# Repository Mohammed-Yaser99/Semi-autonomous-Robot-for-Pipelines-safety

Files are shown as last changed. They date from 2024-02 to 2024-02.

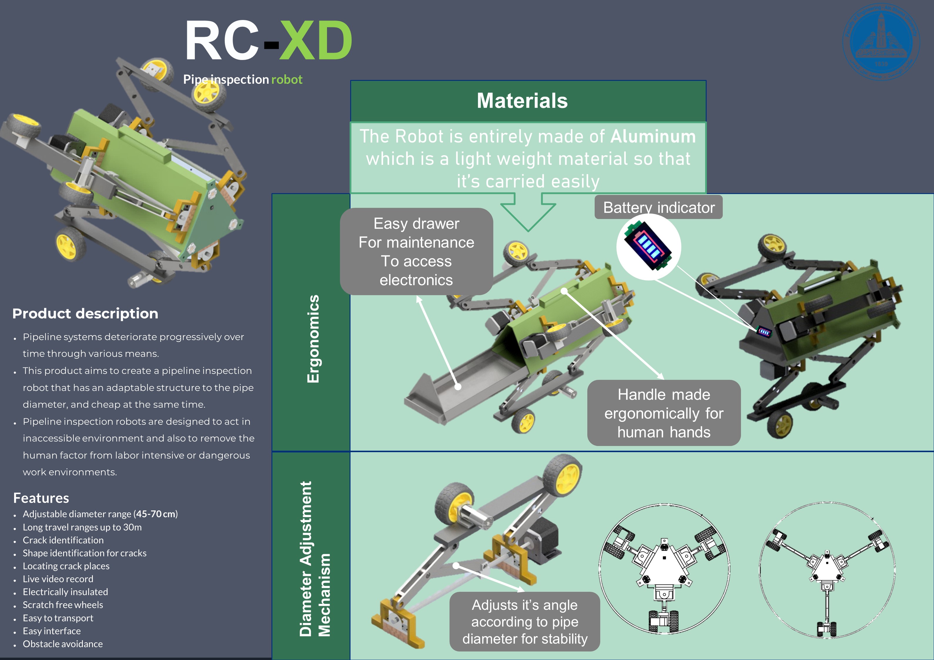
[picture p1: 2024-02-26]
PROJECT's MEDIA/Poster A1-Product Design.jpg

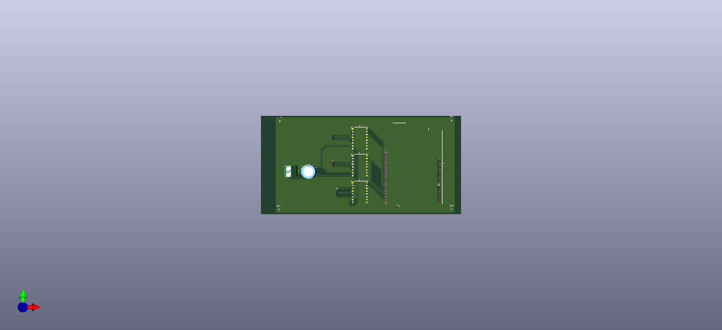
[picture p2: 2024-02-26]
PCB files/Original PCB files ( not manufactured )/pcb 3STEPPERS/3 STEPPERS/FILES/3 STEPPERS.png

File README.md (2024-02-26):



This repository contains working files of a Semi-Autonomous Pipline Inspection robot "RC-XD" :
- Code files for : Arduino mega , Arduino Uno , Rasperry-pi , V-rep simulation
- PCBS design 
- Presenation and Report for detailed aspects and study cases of the project
- Video for the V-rep simulation
  
 
- Pipeline systems deteriorate progressively over time through various means.
- This product aims to create a pipeline inspection robot that has an adaptable structure to the pipe diameter, and cheap at the same time.
- Pipeline inspection robots are designed to act in inaccessible environment and also to remove the human factor from labour intensive or dangerous work environments. 
- Our challenge is to make this robot adaptable to pipe diameters varying from 450mm to 700mm with an adjustable probe mount.

 
- Adjustable diameter range (45-70 cm)
- Long travel ranges up to 30m
- Crack identification 
- Shape identification for cracks 
- Locating crack places
- Live video record 
- Electrically insulated 
- Scratch free wheels and safe to pipes insulation materials 
- Easy to transport 
- Easy interface


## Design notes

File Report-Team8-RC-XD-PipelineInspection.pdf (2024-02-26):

# RESEARCH & PROJECT SUBMISSIONS

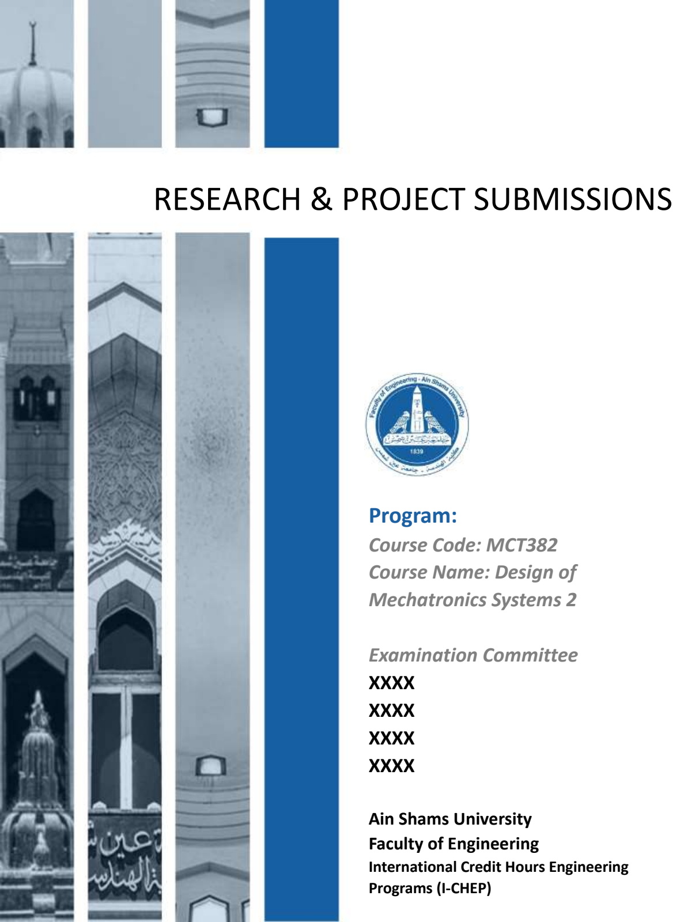
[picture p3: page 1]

SPRING SEMESTER - YEAR 2019/2020

# Program:

## Course Code: MCT382 Course Name: Design of Mechatronics Systems 2

## Examination Committee XXXX XXXX XXXX XXXX

## Ain Shams University Faculty of Engineering

### International Credit Hours Engineering Programs (I-CHEP)

SPRING SEMESTER - YEAR 2019/2020

Student Names:
Mohammed yasser Mohammed
Momen Mohsen
Ahmed Mohammed Nasr

## Student Personal Information for Group Work

## Plagiarism Statement

I certify that this assignment / report is my own work, based on my personal study and/or research and that I have acknowledged all material and sources used in its preparation, whether they are books, articles, reports, lecture notes, and any other kind of document, electronic or personal communication. I also certify that this assignment / report has not been previously been submitted for assessment for another course. I certify that I have not copied in part or whole or otherwise plagiarized the work of other students and / or persons.

Signature/Student Name: | Mohammed Yaser Mohammed
| Momen Mohsen
| Ahmed Mohammed Nasr

Date: 5/5/2021

Student Codes:
17P8214
17P8115
17P8211

AIN SHAMS UNIVERSITY
FACULTY OF ENGINEERING
INTERNATIONAL CREDIT HOURS ENGINEERING PROGRAMS (I-CHEP)

MCT382, Design of Mechatronics Systems 2, SPRING 2020

## Abstract

This report provides basic and advanced operating instructions for the RC-XD Robot. The information in the report will explain the mechanical, electrical and software designs used in this robot, Our vision is to solve some difficulties that pipe inspection companies face, to save the time consumed by manual inspecting procedures and to maintain a safe environment for the employees engaged in this field, Our mission is to improve the quality of the inspecting field in Egypt, to save their time, money and effort and to make robots easily available in the Egyptian market, RC-XD is a pipe inspection robot, it’s main purpose is to inspect the corrosion, cracks , and rust inside the pipes and get its exact position and geometry in the pipe and report it.

## Contents

## List of Figures

## Introduction

Pipeline systems deteriorate progressively over time through various means, so this product aims to create a pipeline inspection robot that has an adaptable structure to the pipe diameter, detects any cracks and cheap at the same time. Pipeline inspection robots are designed to act in inaccessible environment and also to remove the human factor from labour intensive or dangerous work environments. Our challenge is to make this robot adaptable to pipe diameters varying from 450mm to 700mm that can detect any inner cracks in a pipe.

## 1.Market Research

To study the market in Egypt we relied on two sources internet data and face to face meetings with company owners and representatives.

### 1.1. Statistics and surveys

Egyptian market has more than 80 companies in the inspection field excluding petroleum companies, less than 10% of them use robots in their field mainly because it’s too expensive to get a robot from abroad and it’s difficult to maintain it in Egypt.

More than 40% of yearly jobs deal with pipelines with more than 10 meters in length with different diameters ranging from 30cm to 1.2m

A normal inspection job takes 3-4 days in average and average
small companies take 80+ jobs/year.

A technicians’ minimum wage per day ranges from 150 L.E up to 600 L.E, excluding other outlays, so approximately a job with only one technician costs nearly about 2000 L.E

### 1.2. Target

Inspection companies start a job with a site visit to identify what is the required job and take some measurements, then start the solving step which is to brainstorm and think how can they perform this job and what they need, then a preparation step where they gather the required tools and/or operators required, then they start the inspection.

Based on further surveys and meetings, the main target is to eliminate an exhausting and time and money consuming step which is the solving step and eliminating this step will save money, effort and time to a company.

Using these surveys and statistics we concluded how we will shape our robot according to our customers’ needs.

Companies that use robots

Use robots Do not use robots

Figure 1 Companies that use robots relative to all

### 1.3. Value Proposition Canvas

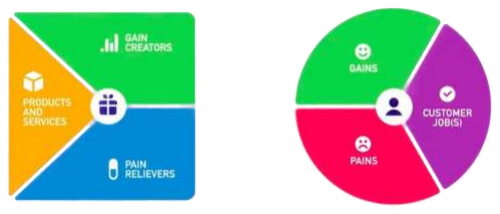
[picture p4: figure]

1.3.1. Gains
- Safe inspection
- Customer Satisfaction
1.3.2. Gain Creators
- Less workers
- Record the inspection process
- More professional method
1.3.3. Pains
- Dealing with hard and extreme cases
- Time and money consuming process
- Unprofessional technicians’ faults
1.3.4. Pain Relievers
- Time efficient
- Less effort
- Adjustable with different diameters
- Crack shape record
1.3.5. Customer Jobs
- Inspection of pipes in oil and gas field
- Case study
1.3.6. Products and Services
- Semi-autonomous
- Adjustable
- Scratch free material
- After sales

Figure 2 Value Proposition canvass

### 1.4. Lean Canvas Model

### 1.5. Academic A1 Poster

Designed for: RC-XD | Designed by: Team 18
Problem 10m+ Length Pipes Diameters variety Insulation Time consuming Existing Alternatives High cost robots Time and money consuming processes | Solution Adjustable Low cost Easy interface Key Metrics Units sold Units rented Contracts | Unique Value Proposition Easy interface Maintenance After Sales Support High-Level Concept | Unfair Advantage Cost Time Channels Sales Team Conferences Company site | Customer Segments Small Gas and Oil inspection companies Early Adopters Below 30 Years old owners
Cost Structure Salaries Development Materials Maintenance | Revenue Structure Contracts Rent Buying

Figure 3 Lean Canvas Model

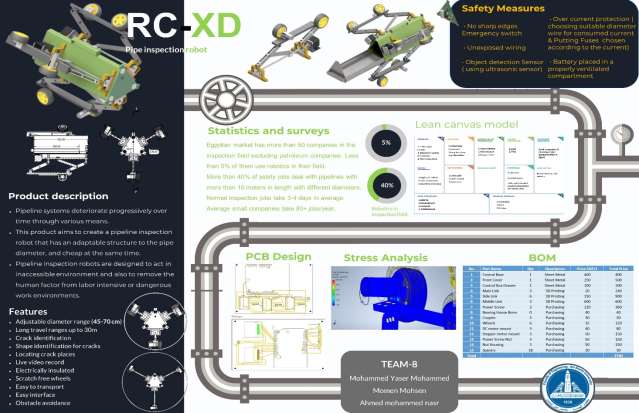
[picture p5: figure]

### 1.6. Product Design A1 Poster

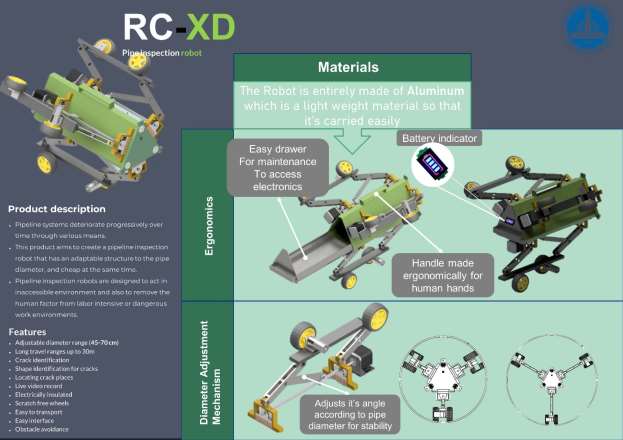
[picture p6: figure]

### 1.5. Brochure

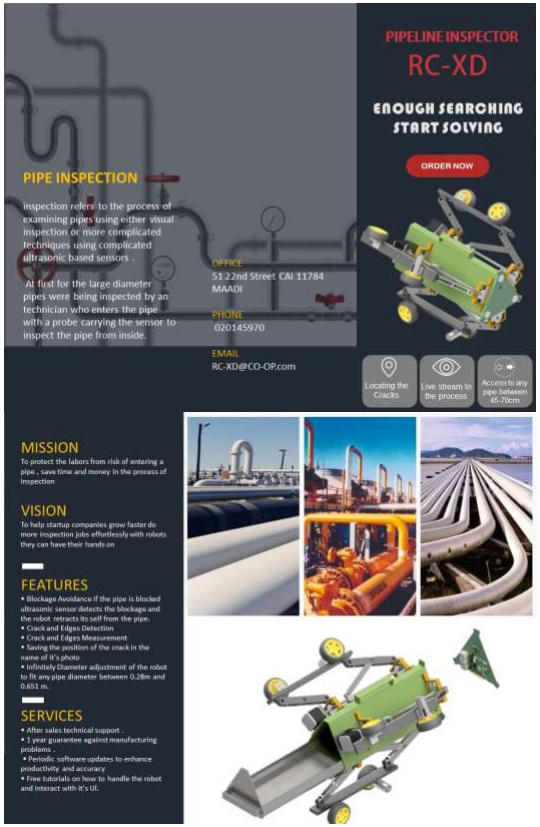
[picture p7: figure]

## 2. Product Description

RC-XD is a semi-autonomous robot that can travel in long pipes with adjustable diameter, scan for inner cracks, locates their locations and identifies the shape of this crack, by setting the pipe diameter, length and the desired travel speed, the robot adjust itself to the pipe diameter and once placed in the pipe it starts to move with the desired speed and begins to scan for any cracks.

RC-XD is a 6 wheeled robot actuated by the four lower wheels, made generally of sheetmetal and do not need an operator to operate it.

### 2.1. Features

- Adjustable diameter range (45-70 cm)
- Long travel ranges up to 30m
- Crack identification
- Shape identification for cracks
- Locating crack places
- Live video record
- Electrically insulated
- Scratch free wheels and safe to pipes insulation materials
- Easy to transport
- Easy interface
- Obstacle avoidance

### 2.2. Environmental Ratings

RC-XD robot is a durable and rugged robot that can be used in harsh environments, well insulated and safe to meet any work site rules.

### 2.3. Main Components

The RC-XD front side contain an ultrasonic sensor behind it the control box which contains the Raspberry Pi, the Arduino uno Launchpad, Lithium ion battery and the PCB, after that we have the main body attached to 3 wheel assemblies with 120⁰ angle between each other -to ensure stability in pipes-each has a mechanism that controls the diameter adjustment. In each mechanism there are 2 wheels, one of those wheels are actuated using a dc motor in the front only, the rest wheels are free to move.

### 2.4. HMI

The user will see the output data as a video feed that can identify any crack and display its dimensions and also the robot will store images of the cracks named with the distance measured and the angle at which the crack was identified

## 3.Mechanical Design

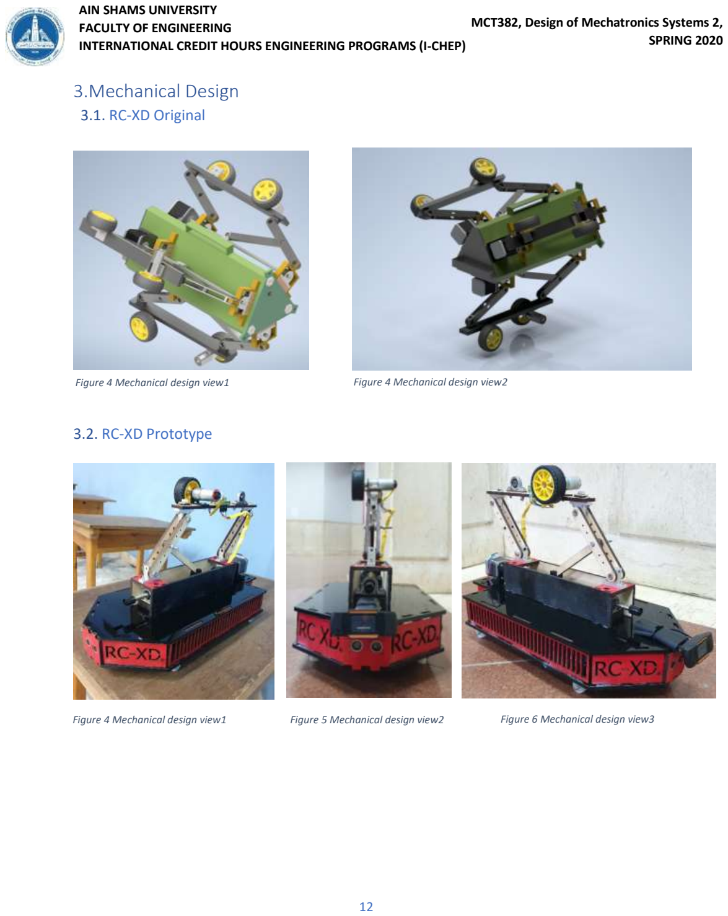
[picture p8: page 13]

### 3.1. RC-XD Original

### 3.2. RC-XD Prototype

Figure 4 Mechanical design view1 | Figure 4 Mechanical design view2
Figure 4 Mechanical design view1 | Figure 5 Mechanical design view2 | Figure 6 Mechanical design view3

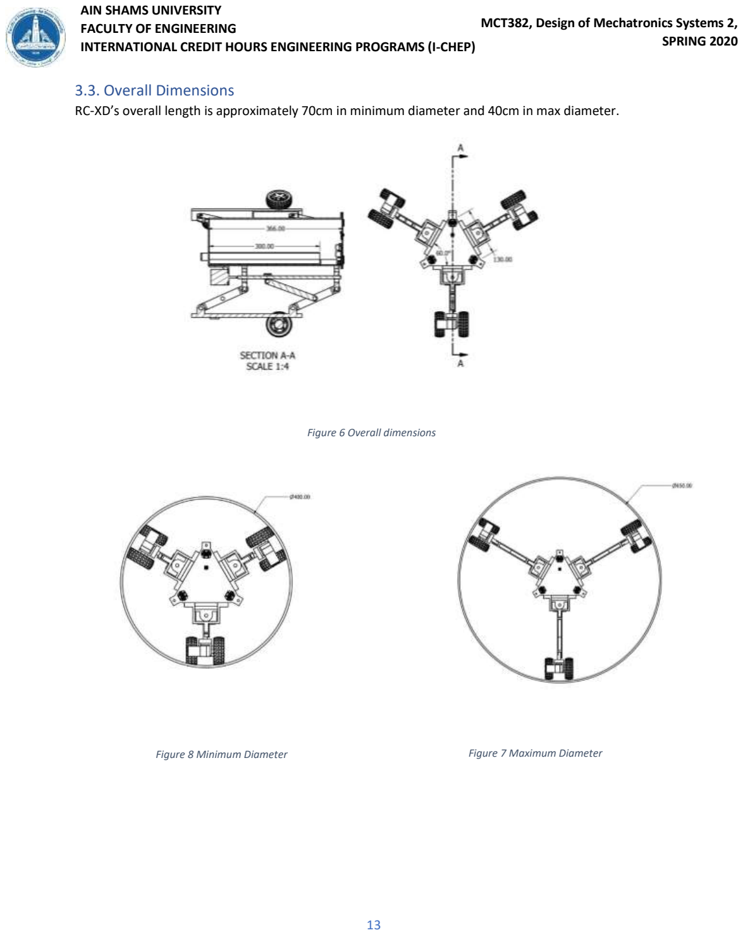
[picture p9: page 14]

### 3.3. Overall Dimensions

RC-XD’s overall length is approximately 70cm in minimum diameter and 40cm in max diameter.

Figure 6 Overall dimensions

Figure 8 Minimum Diameter | Figure 7 Maximum Diameter

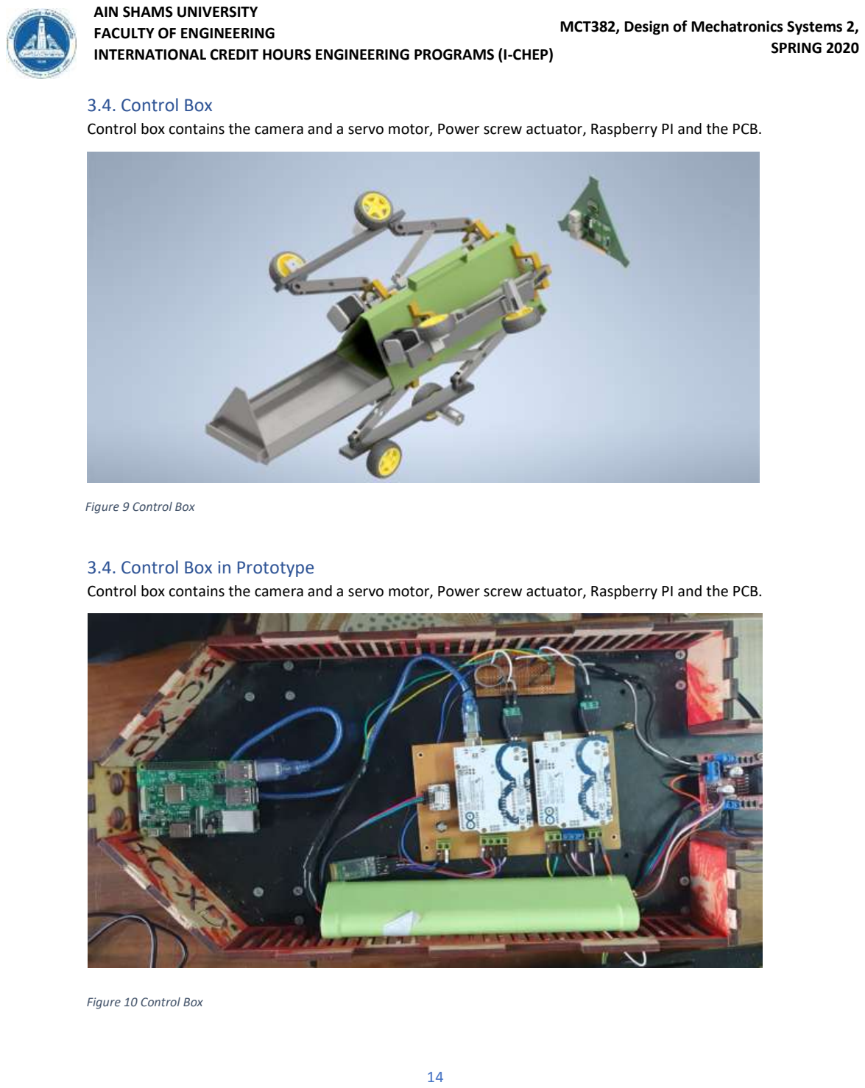
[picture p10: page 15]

### 3.4. Control Box

Control box contains the camera and a servo motor, Power screw actuator, Raspberry PI and the PCB.

### 3.4. Control Box in Prototype

Control box contains the camera and a servo motor, Power screw actuator, Raspberry PI and the PCB.

Figure 9 Control Box

Figure 10 Control Box

### 3.5. Diameter Adjustment Mechanism

In a nutshell it’s a Four-Bar Mechanism actuated by a Four-Bar Mechanism. The power screw actuator receives a signal with the desired diameter, then the power screw rotates with the set angle moving the bushes a certain distance, and the bushed moves a triangular plate attached to it that moves relative to a fixed plate bolted to the base.

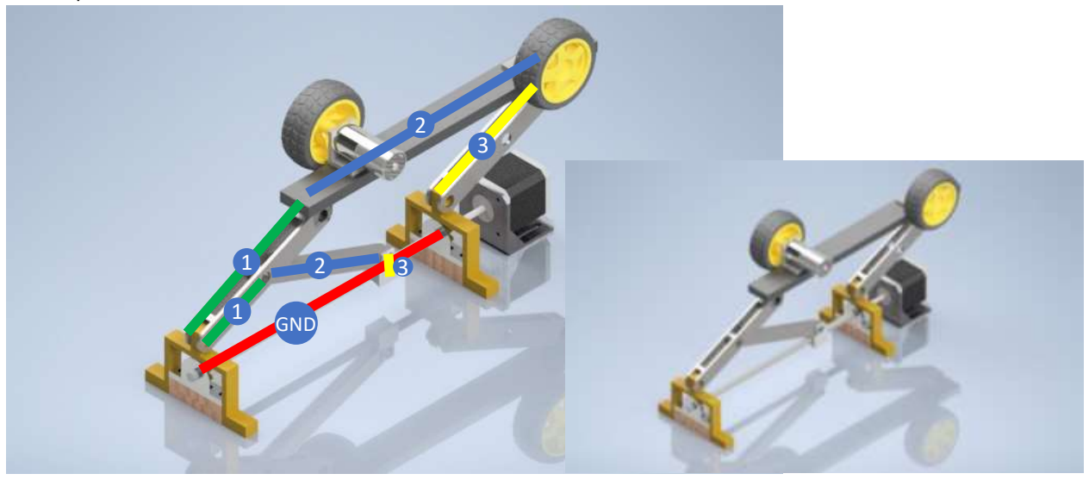
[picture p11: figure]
GND

Attached to the moving plate three links connected to the arms holding the wheels so moving the power screw nut changes the angle of the hinged arms changing the central distance of the wheel.

Figure 13 Diameter Adjustment Mechanism

### 3.6. Stress Analysis

Assuming Worst Case:

- Robot’s weight is 10 kg
- Only two wheel carries the whole weight
- Motor Radial Load = 60 N.m (From datasheet)

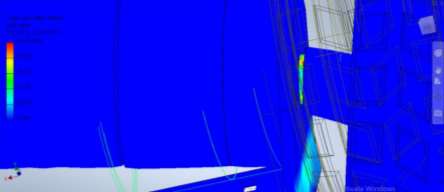
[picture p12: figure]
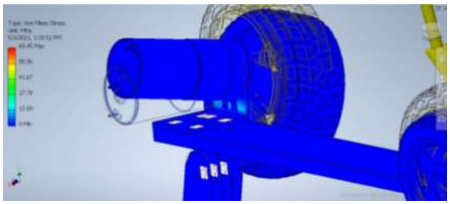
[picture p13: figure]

Figure 14 Stress Analysis

Figure 15 Stress Analysis

### 3.7. Mechanical BOM

No. | Part Name | Qty | Description | Price EGP/1 | Total Price
1 | Central Base | 1 | Sheet Metal | 400 | 400
2 | Front Cover | 1 | Sheet Metal | 250 | 500
3 | Control Box Drawer | 1 | Sheet Metal | 100 | 200
4 | Main Link | 3 | 3D Printing | 20 | 240
5 | Side Link | 6 | 3D Printing | 150 | 900
6 | Middle Link | 3 | 3D Printing | 600 | 600
7 | Power Screw | 3 | Purchasing | 120 | 360
8 | Bearing House 8mm | 0 | Purchasing | 40 | 40
9 | Coupler | 3 | Purchasing | 30 | 30
10 | Wheels | 6 | Purchasing | 15 | 120
11 | DC motor mount | 3 | Purchasing | 40 | 80
12 | Stepper motor mount | 3 | Purchasing | 50 | 150
13 | Power Screw Nut | 3 | Purchasing | 50 | 150
14 | Nut Housing | 3 | Purchasing | 50 | 150
15 | Spacers | 18 | Purchasing | 30 | 30
Total | | | | | 3760
Figure 11 Mechanical BOM

## 4. Electrical Design

Electrical Schematics is designed to fit the operation principles determined and depends on the actuator sizing that was done will be mentioned later, and the selected sensors, so the battery was roughly estimated. And the calculations determined that a 12V battery of 6000mAh is required.

So, to limit the size and weight we decided to use Lithium ions batteries and its characteristics also suits our needs.

### 4.1. Sensors Selection

RC-XD uses five sensors, three encoders for each motor for position feedback, one camera to detect the cracks and an ultrasonic sensor to detect obstacles if there is any.

4.1.2. Raspberry PI Camera NV
Raspberry Pi Night Vision Camera plugs directly into the CSI connector on the Raspberry Pi.

This Raspberry Pi night vision camera uses the same OV5647 as the standard Raspberry Pi camera, and is therefore able to deliver a crystal clear 5MP resolution image, or 1080p HD video recording at 30fps.

4.1.3. DC Motor Encoder
Attached to each DC Motor is an encoder which transmits a set number of electronic pulses for each rotation of its shaft so by using simple mathematical formulas it is easy to calculate the travelled distance.

### 4.2. Actuator Sizing

Estimated total weight from CAD is 10 kg driven by two DC motors and the two actuated wheels have the same parameters and conditions.

Wheel outer diameter = 66 mm

Assumed wheel mass = 0.3 kg

Rolling Coefficient of friction between wheel and pipe = 0.3

Assume all pipes has no inclination.

Assumed fixed speed operation = 2 rad/sec

tacc= 1 sec

Jtot=Jm+Jeff (on each actuated wheel)

### Jactuated wheel = (0.5*m*r^2)=(0.5*0.3* (66 × 10⁻³

/ 2)²

)= 1.6335*10⁻⁴

### kg·m ²

Using kinetic conversion theorem:

### - Jbody = m*r²=10*(66 × 10⁻³

/ 2)²= 10.89*10⁻³

### kg·m ² - Jrolling wheel = 0.5*m*r²= 0.5*0.3* (66 × 10⁻³

/ 2)²= 1.6335*10⁻⁴

### kg·m ²

### Jeff = 1.6335*10⁻⁴

+ 10.89*10⁻³

+ 1.6335*10⁻⁴ = 11.22*10⁻³

### Jtot=Jm+Jeff = 11.22*10⁻³ + 11.22*10⁻³ = 0.02243 kg·m ²

### Tr (assumed resistive torque) = 9.8(5+(0.3*3))*0.3* (66 × 10⁻³

/ 2) = 0.57 Nm

Θ

### acc = 2/0.1=20 rad/sec

### Peak torque required = Tmax = 0.02243*20 + 0.57 = 1.5 Nm

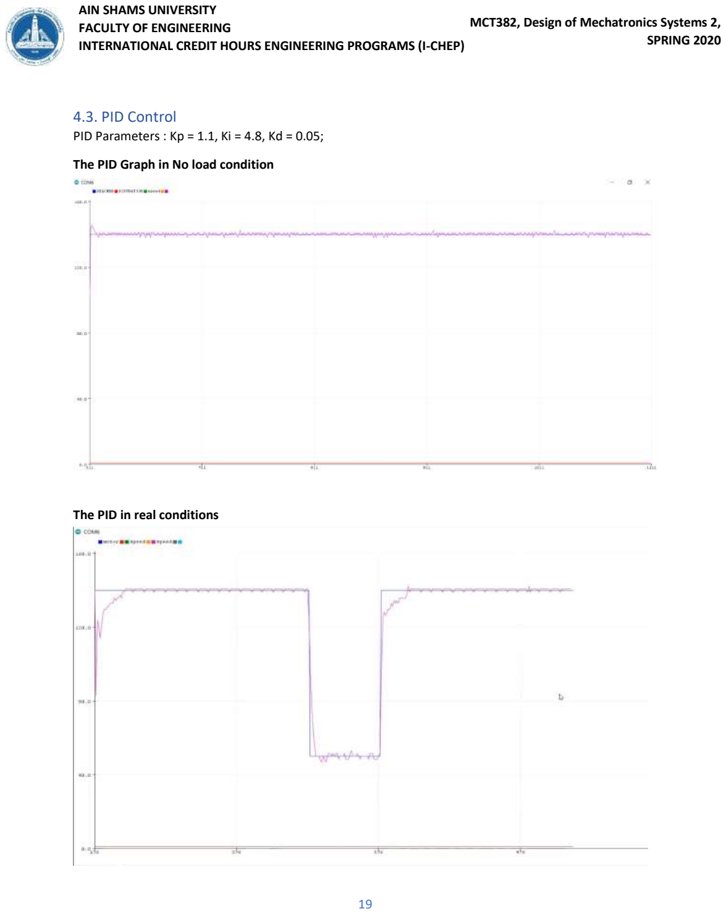
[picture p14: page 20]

### 4.3. PID Control

PID Parameters : Kp = 1.1, Ki = 4.8, Kd = 0.05;

The PID Graph in No load condition

The PID in real conditions

### 4.4. Battery Sizing

Average current draw by each component:

- | Arduino uno board | 0.05 A
- | Raspberry pi | 2.5 A
- | Three driving DC motors | 3.5 A
- | Power screw three Stepper motor | 5.25 A
- | Ultrasonic sensor | 0.015A
- | Camera | 0.5A

For motors I(amp) = (Nω*2π/V*60)

Consumed Power = ((0.05+2.5+0.015+0.5)*5) +((3.5+5.25)*12) = 120 W

Assumed total power losses 10 W

Total power = 130 W

Battery Voltage 12V

Total current = 10 A

Operating time 30 minutes

### Battery size needed = 5 Ah

### 4.5.PCB Design

4.5.1. PCB Schematic

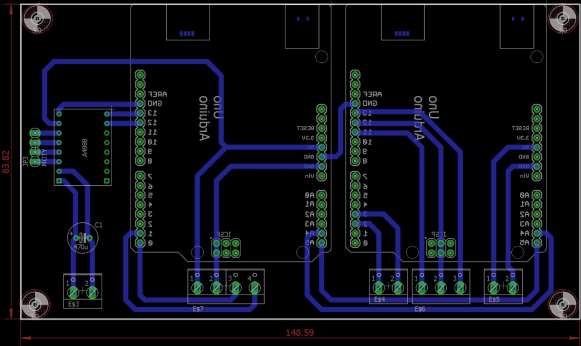
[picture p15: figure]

4.5.2. Communication Protocols
- Arduino1 controls the stepper motor and the bluetooth module
- Arduino2 controls the Dc Motors with the pid control
- Raspberry pi controls the camera with the image processing

We tried to optimize our resources and use the different communication protocols available in the uno. So Arduino1 takes the diameter and distance commands from a mobile application using the Bluetooth module using UART, then it sends the data to Arduino2 using I2C protocol to begin moving the report, and in parallel the raspberry pi vision module works and when a crack is detected it sends a character to Arduino2 using UART to slow down to be able to see the crack.

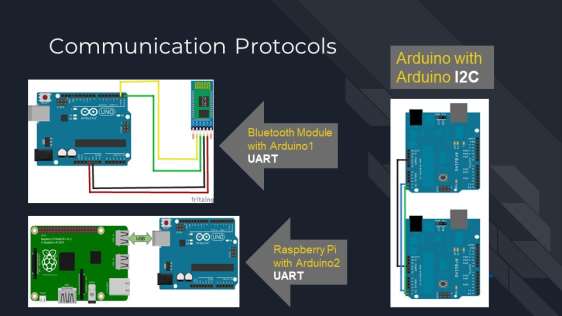
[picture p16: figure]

### 4.6. Electrical BOM

Figure 12 Electrical BOM

No. | Part Name | Qty | Price EGP/1 | Total Price
1 | Raspberry PI | 1 | 1250 | 1250
2 | DC Motor | 3 | 200 | 600
3 | Ultrasonic Sensor | 1 | 45 | 45
4 | PI Camera | 1 | 450 | 450
5 | Battery | 1 | 750 | 750
6 | Charging Port | 1 | 50 | 50
7 | Start/Stop Button | 2 | 20 | 40
8 | Arduino uno | 1 | 160 | 160
9 | PCB | 1 | 200 | 200
10 | Battery Indicator | 1 | 50 | 50
11 | DC Motor driver | 3 | 95 | 285
12 | Stepper driver | 3
13 | Encoder | 3 | 100 | 300
14 | LED | 3
15 | Stepper motor | 3 | 100 | 300
Total | | | | 3500

## 6. MAIN CODE

RC-XD’s main purpose is to identify any crack, locate its position, get its shape and save photos named with the identified crack position and degree with its dimensions.

Our code is responsible for all RC-XD’s functions, defining crack dimensions and recognizing any crack located inside a pipe.

### 6.1 FlowChart

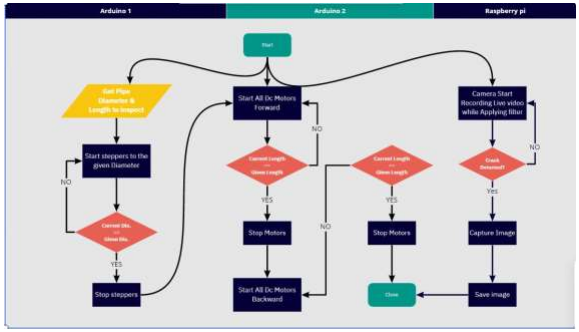
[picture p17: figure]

6.1.1 Crack Recognition

# Python program to explain cv2.imshow() method

# importing cv2

from scipy.spatial import distance as dist import numpy as np
import cv2
from imutils import perspective
from imutils import contours import imutils
#from serial import Serial import serial

import time

if __name__ == '__main__':
ser = serial.Serial('/dev/ttyACM0', 9600, timeout=1) | #Open port with
| baud rate

# capture frames from a camera

cap = cv2.VideoCapture(0)

pixelsPerMetric =3.139

def midpoint(ptA, ptB):
return ((ptA[0] + ptB[0]) * 0.5, (ptA[1] + ptB[1]) * 0.5)

num=1

# loop runs if capturing has been initialized while (1):

# reads frames from a camera

ret, frame = cap.read()

# converting BGR to HSV

# Reading same image in another

# variable and converting to gray scale.

gray = cv2.cvtColor(frame, cv2.COLOR_RGB2GRAY)
gray = cv2.GaussianBlur(frame, (7, 7), 0)

# canny fcn is used to detect the edges if the image has no edges it produce a

# none image (black) , but if edges were detected in marks the edges with white color

edges = cv2.Canny(gray, 0, 255)

edges = cv2.dilate(edges, None, iterations=15) edges = cv2.erode(edges, None, iterations=15)

# Display an original image

cv2.imshow('Original', frame) #uncomment to see the original window frame

# discovers edges in the input image image and

# marks them in the output map edges

edges = cv2.Canny(frame, 100, 200)

# Display edges in a frame

cv2.imshow('Edges', edges)

# image color check to see if edges exist after canny fcn if cv2.countNonZero(edges) == 0:

print("Image has no edges")
else:
print("detected edges in the image") ser.write('q'.encode('utf-8'))
time.sleep(1)
# contourin the found edges

(cnts, _) = cv2.findContours(edges.copy(), cv2.RETR_TREE,
| cv2.CHAIN_APPROX_SIMPLE)
(cnts, _) = contours.sort_contours(cnts)

count = 1
# Going through every contours found in the image.

for c in cnts:
# if the contour is not sufficently large, ignore it if cv2.contourArea(c) < 100:

continue

# compute the rotated bounding box of the contour orig = frame.copy()

box = cv2.minAreaRect(c)
box = cv2.cv.BoxPoints(box) if imutils.is_cv2()
else cv2.boxPoints(box)
box = np.array(box, dtype="int")
cv2.drawContours(orig, [box.astype("int")], -1, (0, 255, 0), 2) box = perspective.order_points(box)

for (x, y) in box:
cv2.circle(orig, (int(x), int(y)), 5, (0, 0, 255), -1)

(tl, tr, br, bl) = box
(tltrX, tltrY) = midpoint(tl, tr)
(blbrX, blbrY) = midpoint(bl, br)

(tlblX, tlblY) = midpoint(tl, bl)
(trbrX, trbrY) = midpoint(tr, br)

cv2.circle(orig, (int(tltrX), int(tltrY)), 5, (255, 0, 0), -1) cv2.circle(orig, (int(blbrX), int(blbrY)), 5, (255, 0, 0), -1) cv2.circle(orig, (int(tlblX), int(tlblY)), 5, (255, 0, 0), -1) cv2.circle(orig, (int(trbrX), int(trbrY)), 5, (255, 0, 0), -1) cv2.line(orig, (int(tltrX), int(tltrY)), (int(blbrX), int(blbrY)),
| (255, 0, 255), 2)
cv2.line(orig, (int(tlblX), int(tlblY)), (int(trbrX), int(trbrY)),
| (255, 0, 255), 2)

dA = dist.euclidean((tltrX, tltrY), (blbrX, blbrY))
dB = dist.euclidean((tlblX, tlblY), (trbrX, trbrY))

dimA = dA / pixelsPerMetric
dimB = dB / pixelsPerMetric

cv2.putText(orig, "D1 = {:.1f}mm".format(dimA), (int(20), int(20)), cv2.FONT_HERSHEY_SIMPLEX,
| 0.65, (255, 100, 122), 2)
cv2.putText(orig, "D2 = {:.1f}mm".format(dimB), (int(20), int(50)), cv2.FONT_HERSHEY_SIMPLEX,
| 0.65, (255, 100, 122), 2)
cv2.imwrite("frame%d.jpeg" %num,orig) | # save frame as JPEG file
num += 1
k = cv2.waitKey(5) & 0xFF
if k == 27:
break | # exit if Escape is hit# press for Esc key to stop | or close
| the window

# Close the window

cap.release()

### Here are some output samples saved for random crack pictures for testing:

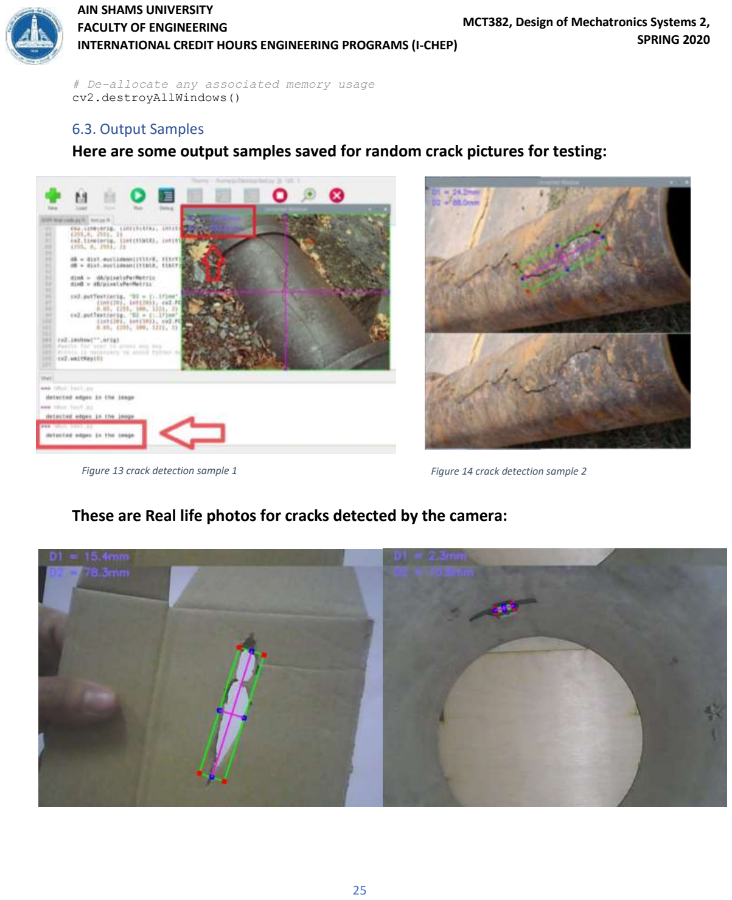
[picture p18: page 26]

# De-allocate any associated memory usage cv2.destroyAllWindows()

### 6.3. Output Samples

### These are Real life photos for cracks detected by the camera:

Figure 13 crack detection sample 1 | Figure 14 crack detection sample 2

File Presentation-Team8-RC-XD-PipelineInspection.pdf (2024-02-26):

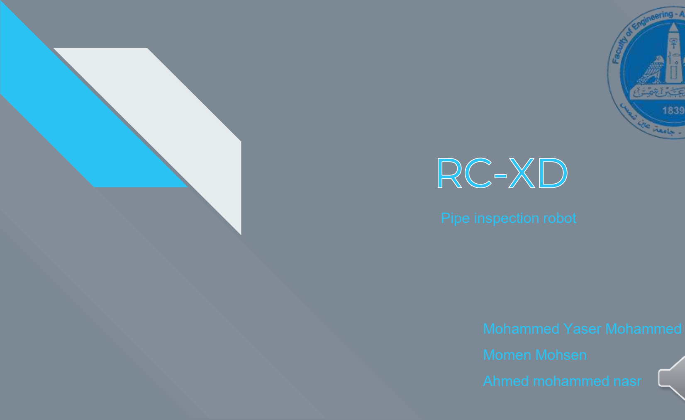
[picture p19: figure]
Mohammed Yaser Mohammed; Momen Mohsen; Ahmed mohammed nasr; Pipe inspection robot

# TOC

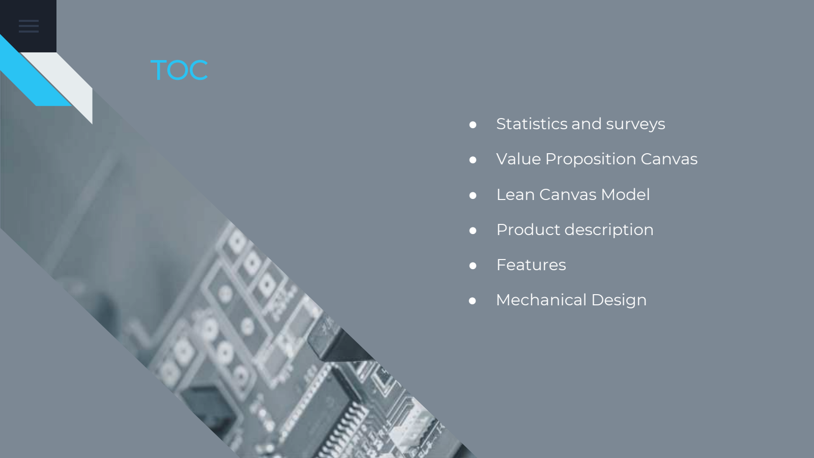
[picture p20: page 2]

- Product description
- Features
- Mechanical Design
- Value Proposition Canvas
- Lean Canvas Model
- Statistics and surveys

- Egyptian market has more than 50 companies in the inspection
- Less than 5% of them use robotics in their field.
- More than 40% of yearly jobs deal with pipelines with more than 10

meters in length with different diameters.

- Normal inspection jobs take 3-4 days in average.
- Average small companies take 80+ jobs/year.

# Value Proposition Canvas

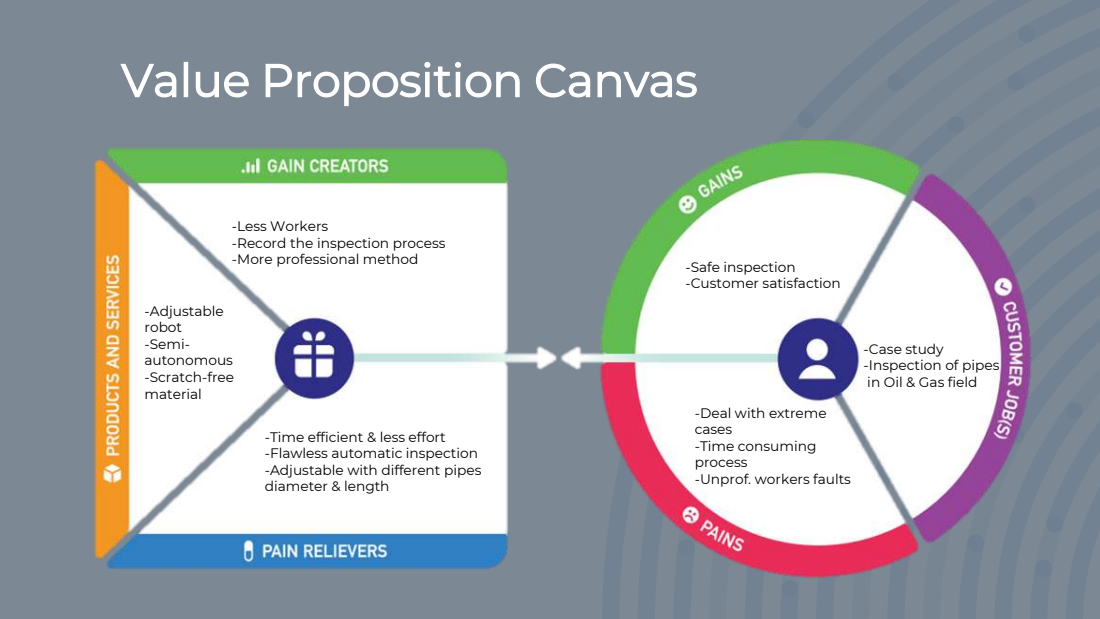
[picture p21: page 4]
-Adjustable robot -Semi- autonomous -Scratch-free material; -Safe inspection -Customer satisfaction

-Less Workers
-Record the inspection process
-More professional method

-Case study
-Inspection of pipes
in Oil & Gas field

-Deal with extreme
cases
-Time consuming
process
-Unprof. workers faults

-Time efficient & less effort
-Flawless automatic inspection
-Adjustable with different pipes
diameter & length

# Lean canvas model

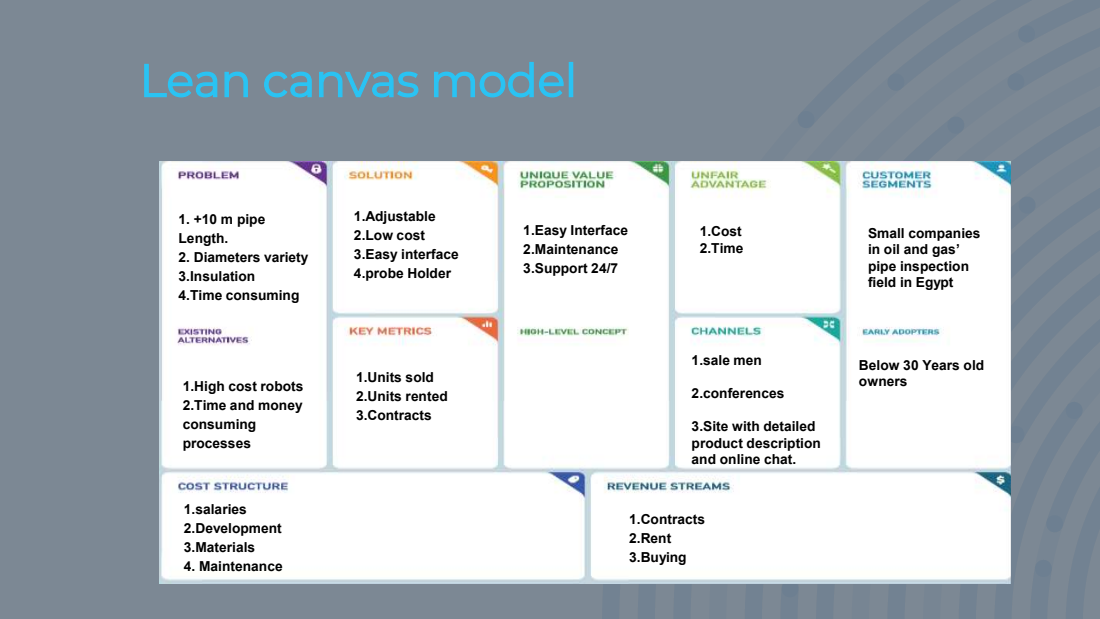
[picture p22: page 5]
1. +10 m pipe Length. 2. Diameters variety 3.Insulation 4.Time consuming; 1.Adjustable 2.Low cost 3.Easy interface 4.probe Holder; 1.Units sold 2.Units rented 3.Contracts; 1.Easy Interface 2.Maintenance 3.Support 24/7; 1.Cost 2.Time; 1.sale men; 2.conferences; 1.salaries 2.Development 3.Materials 4. Maintenance; 1.Contracts 2.Rent 3.Buying

Small companies
in oil and gas’
pipe inspection
field in Egypt

Below 30 Years old
owners

1.High cost robots
2.Time and money
consuming
processes

3.Site with detailed
product description
and online chat.

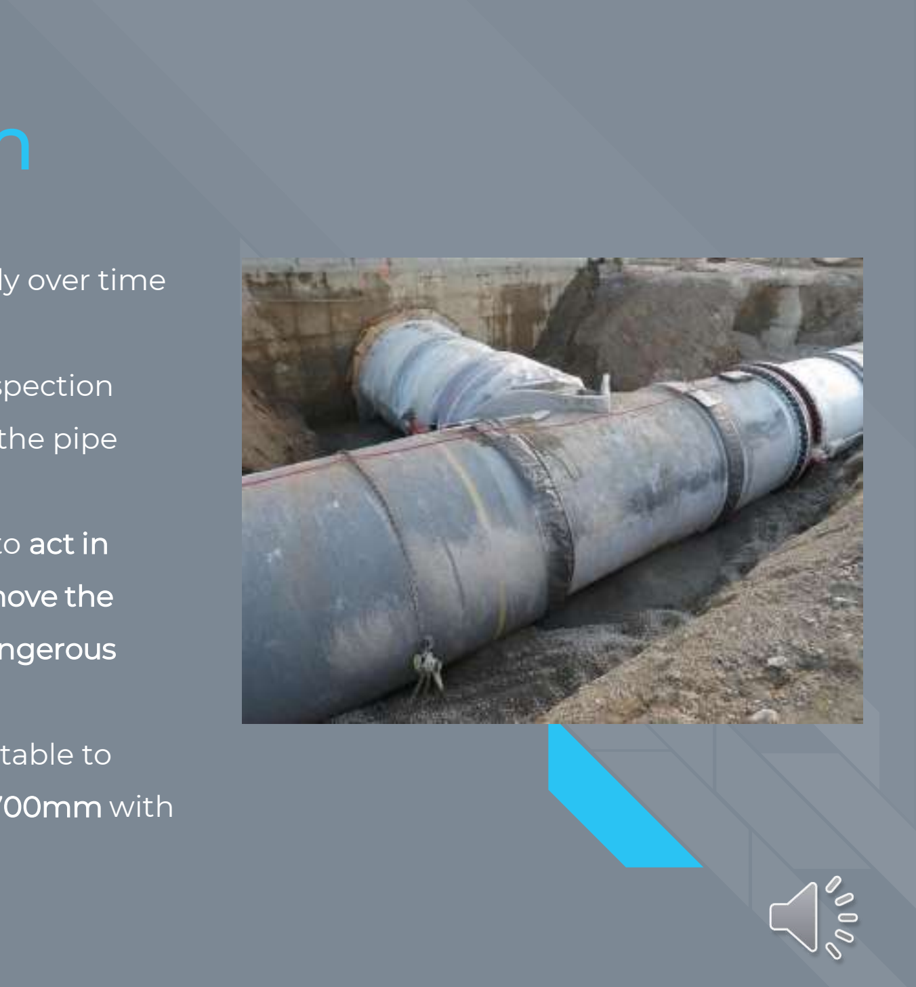
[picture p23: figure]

# Product description

- Pipeline systems deteriorate progressively over time through various means.
- This product aims to create a pipeline inspection robot that has an adaptable structure to the pipe diameter, and cheap at the same time.
- Pipeline inspection robots are designed to act in inaccessible environment and also to remove the human factor from labour intensive or dangerous work environments.
- Our challenge is to make this robot adaptable to pipe diameters varying from 450mm to 700mm with an adjustable probe mount.

# Features

- Adjustable diameter range (45-70 cm)
- Long travel ranges up to 30m
- Crack identification
- Shape identification for cracks
- Locating crack places
- Live video record
- Electrically insulated
- Scratch free wheels and safe to pipes insulation materials
- Easy to transport
- Easy interface

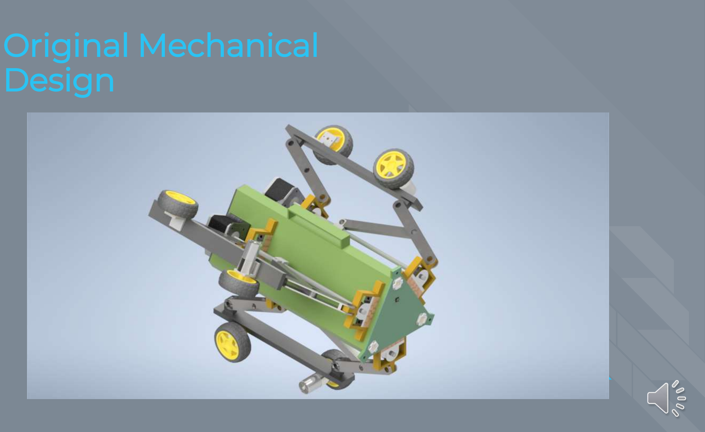
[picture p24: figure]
Original Mechanical Design

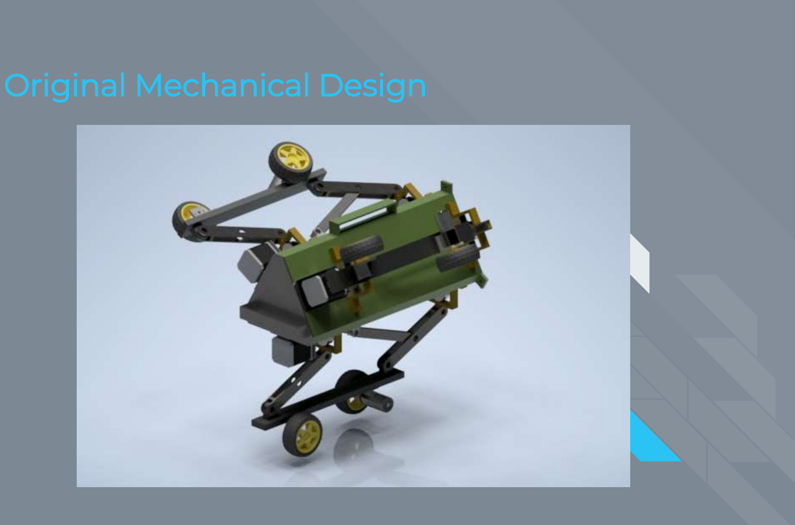
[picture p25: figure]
Original Mechanical Design

# Prototype Mechanical Design

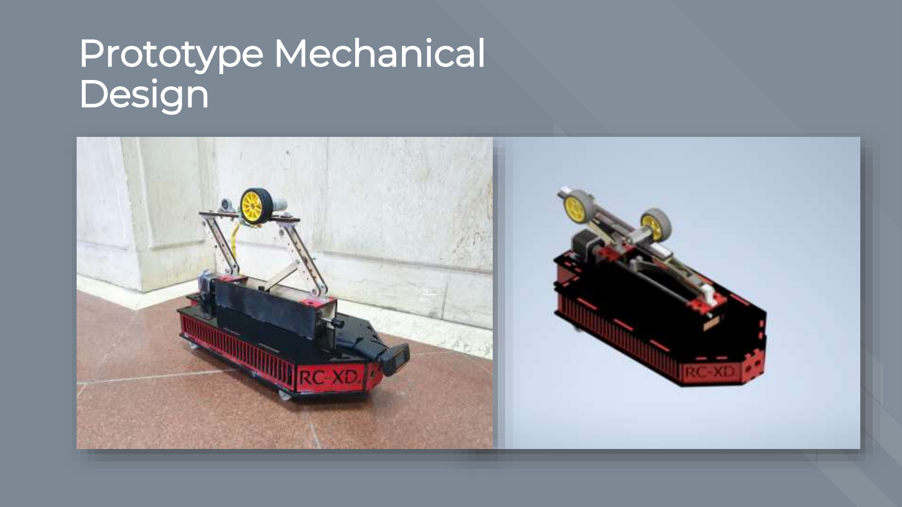
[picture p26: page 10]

Main Body Working Drawing

- In sheet Metal working drawings aren’t needed as it Is made by laser cutting and bending machines , so they require either a PDF file or a Dxf. file - in order to get the flat pattern view - according to the manufacturer

Overall Dimensions

Maximum Diameter

Minimum Diameter

# Diameter Adjustment Mechanism

In a nutshell we used a 4bar mechanism to actuate a 4bar mechanism.

- The power screw rotates with the set angle moving the bushes a certain distance.
- The bushes moves a rectangular link attached to it that moves relative to a hinged link in the joint fixed to the base.
- Attached to the moving links the main link connected to the arms holding the wheels so moving the link changes the angle of the hinged links changing the central distance of the wheel.

# Wheel Assembly


- DC motor is bolted with a L-stand with M4 bolts and then both are bolted with the main link.
- Rubber wheels are used to protect the pipes from scratches


# Stress Analysis

Assuming Worst Case:
- Robot’s weight is 10 kg
- Only two wheel carries the whole weight
- Motor Radial Load = 60 N.m (From datasheet)
- Minimum safety factor of 5 which pretty safe

# Mechanical BOM

No. | Part Name | Qty | Description | Price EGP/1 | Total Price
1 | Central Base | 1 | Sheet Metal | 400 | 400
2 | Front Cover | 1 | Sheet Metal | 250 | 500
3 | Control Box Drawer | 1 | Sheet Metal | 100 | 200
4 | Main Link | 3 | Sheet Metal | 20 | 240
5 | Side Link | 6 | Sheet Metal | 150 | 900
6 | Middle Link | 3 | Sheet Metal | 600 | 600
7 | Power Screw | 3 | Purchasing | 120 | 360
8 | Bearing House 8mm | 0 | Purchasing | 40 | 40
9 | Coupler | 3 | Purchasing | 30 | 30
10 | Wheels | 6 | Purchasing | 15 | 120
11 | DC motor mount | 3 | Purchasing | 40 | 80
12 | Stepper motor mount | 3 | Purchasing | 50 | 150
13 | Power Screw Nut | 3 | Purchasing | 50 | 150
14 | Nut Housing | 3 | Purchasing | 50 | 150
15 | Spacers | 18 | Purchasing | 30 | 30
Total

Control Box

- Control box contains the PCB & the Battery.
- While the raspberry pi is attached to the front cover.


Fan to ventilate
the electric parts
inside

# Actuator Sizing

# PID GRAPHS


- PID In no load condition
- PID In normal loading conditions

PCB Board

PCB Board in Real Life

# Electrical BOM

No. | Part Name | Qty | Price EGP/1 | Total Price
1 | Raspberry PI | 1 | 1250 | 1250
2 | DC Motor | 3 | 200 | 600
4 | PI Camera | 1 | 450 | 450
5 | Battery | 1 | 750 | 750
6 | Charging Port | 1 | 50 | 50
7 | Start/Stop Button | 2 | 20 | 40
8 | Arduino uno | 2 | 160 | 320
9 | PCB | 1 | 200 | 200
Total | | | | 3500

# Electrical Design

Sensor Selection:

- RC-XD uses five sensors, three encoders for each motor for position feedback, one camera to detect the cracks and an ultrasonic to detect blockage in pipes.

Used Sensors:

- Raspberry PI Camera NV
- Ultrasonic sensor
- DC Motor Encoder

Simulation in SW

# Communication Protocols

## Arduino with


Bluetooth Module
with Arduino1
UART

Raspberry Pi
with Arduino2
UART

## Arduino I2C

# Vision

- RC-XD’s main purpose is to identify any crack, locate its position, get its shape and save photos named with the identified crack position and degree with its dimensions.
- Test Case Photos
- Real Case Photos

# V-REP Simulation


## Full Functioning Prototype Video Test Cases



# Thank you!

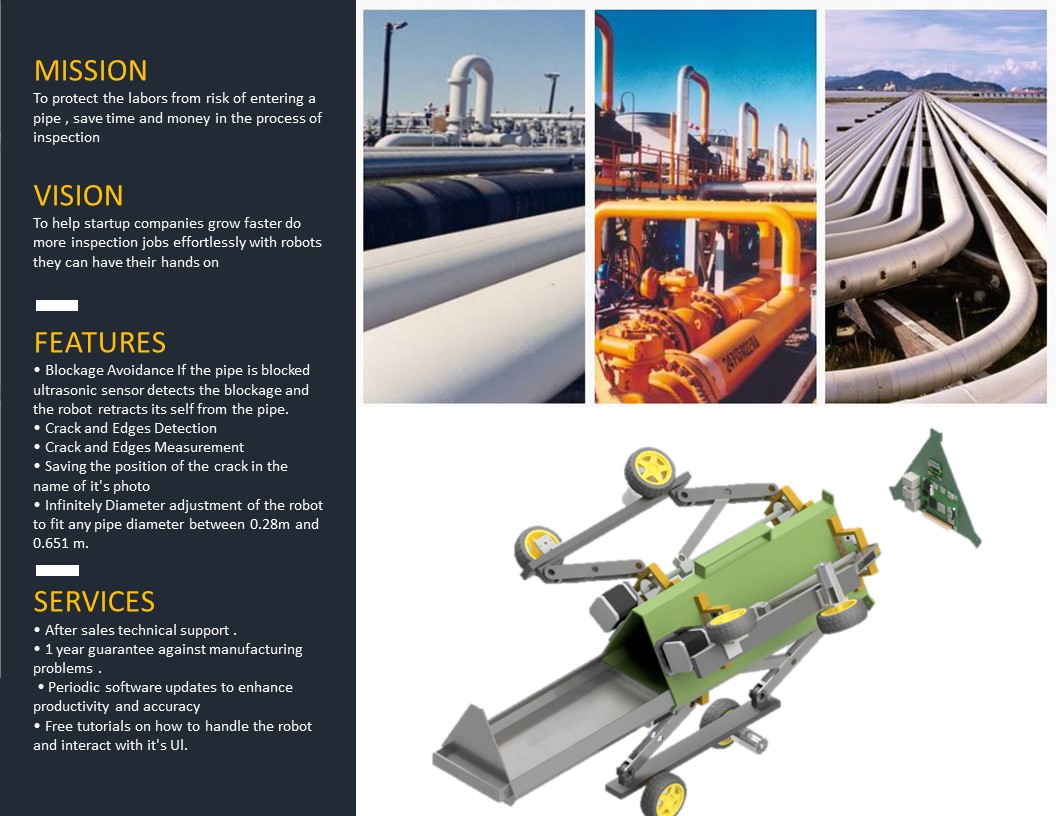
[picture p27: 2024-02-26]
PROJECT's MEDIA/Brochure/Slide2.JPG

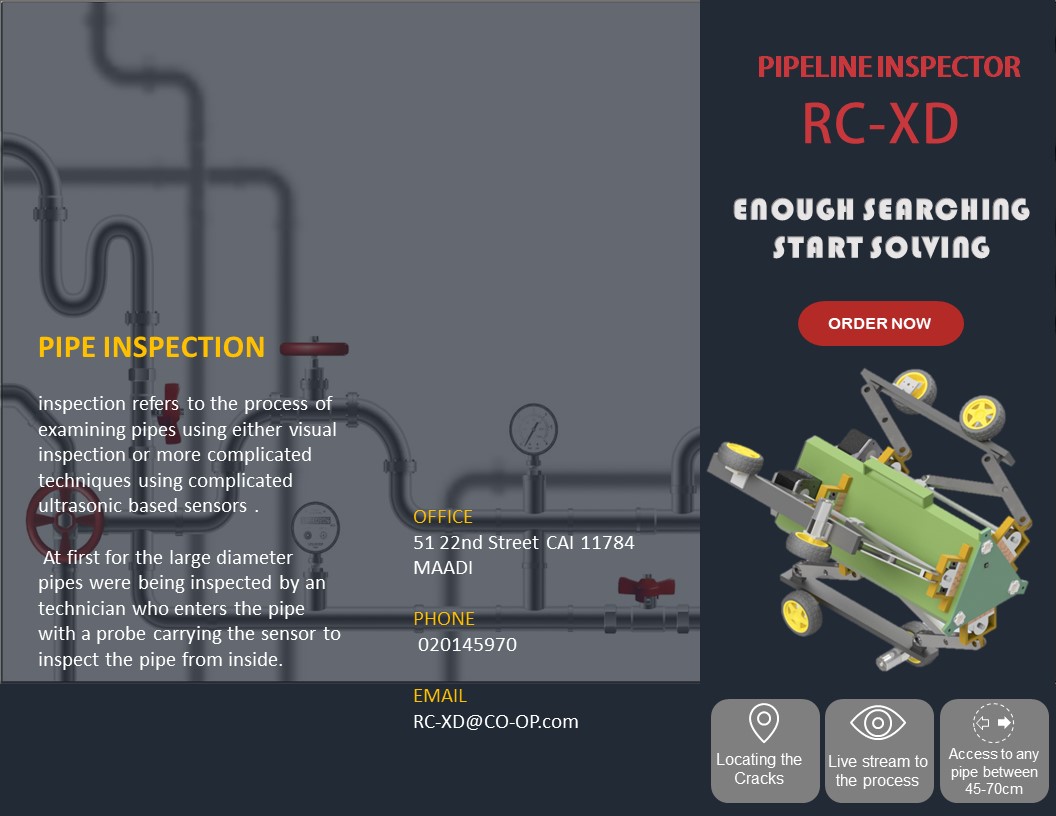
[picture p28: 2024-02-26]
PROJECT's MEDIA/Brochure/Slide1.JPG

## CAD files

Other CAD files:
PCB files/Original PCB files ( not manufactured )/pcb 3STEPPERS/3 STEPPERS/FILES/OldVersions/3 STEPPERS.0001.iam
PCB files/Original PCB files ( not manufactured )/pcb 3STEPPERS/3 STEPPERS/FILES/OldVersions/CP_Radial_D12.5mm_P7.50mm.0001.iam
PCB files/Original PCB files ( not manufactured )/pcb 3STEPPERS/3 STEPPERS/FILES/OldVersions/PinHeader_1x06_P2.54mm_Vertical.0001.iam
PCB files/Original PCB files ( not manufactured )/pcb 3STEPPERS/3 STEPPERS/FILES/OldVersions/PinHeader_1x08_P2.54mm_Vertical.0001.iam
PCB files/Original PCB files ( not manufactured )/pcb 3STEPPERS/3 STEPPERS/FILES/OldVersions/PinHeader_1x10_P2.54mm_Vertical.0001.iam
PCB files/Original PCB files ( not manufactured )/pcb 3STEPPERS/3 STEPPERS/FILES/OldVersions/PinSocket_1x04_P1.00mm_Vertical.0001.iam
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

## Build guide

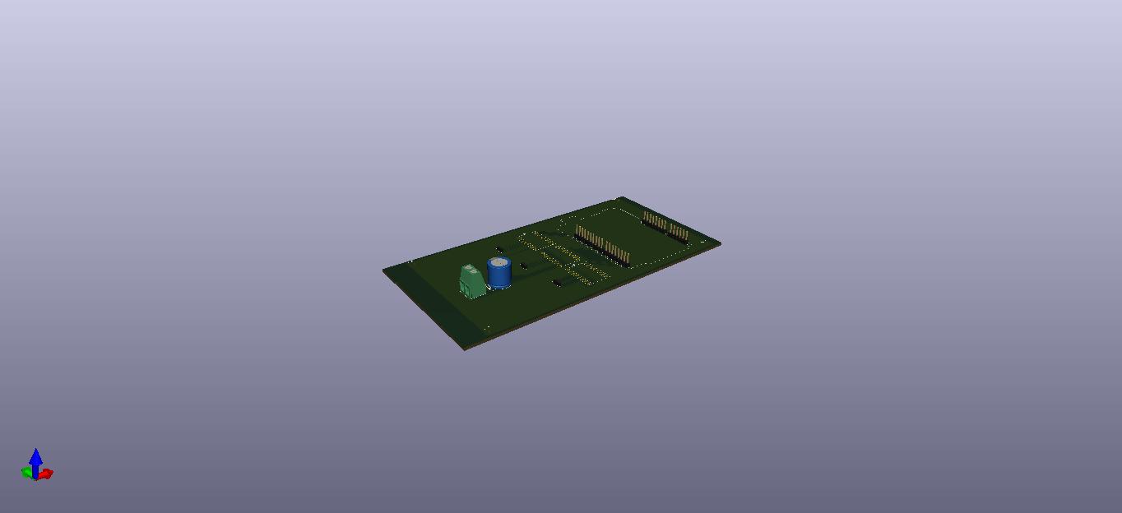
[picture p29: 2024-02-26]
PCB files/Original PCB files ( not manufactured )/pcb 3STEPPERS/3 STEPPERS/FILES/3 STEPPERS.jpg

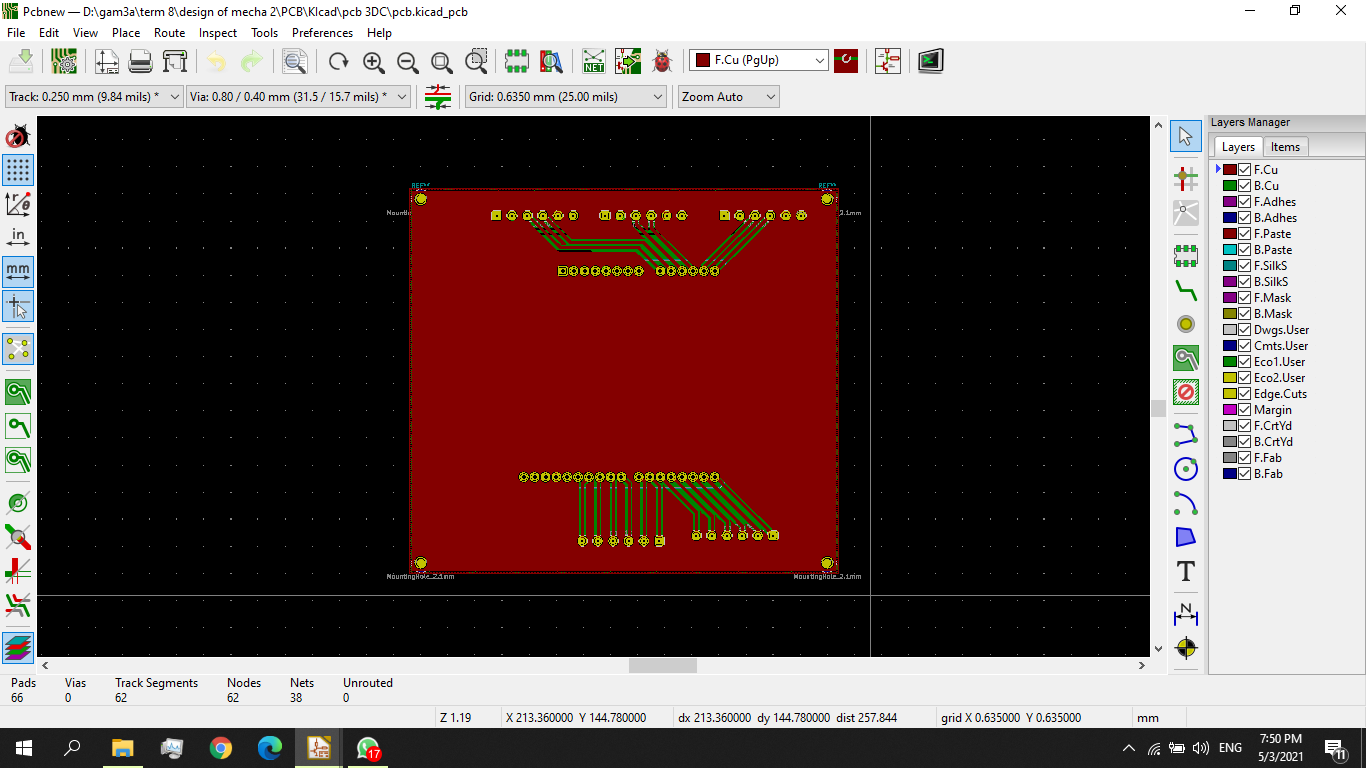
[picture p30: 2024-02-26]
PCB files/Original PCB files ( not manufactured )/pcb 3DC/Screenshot (64).png

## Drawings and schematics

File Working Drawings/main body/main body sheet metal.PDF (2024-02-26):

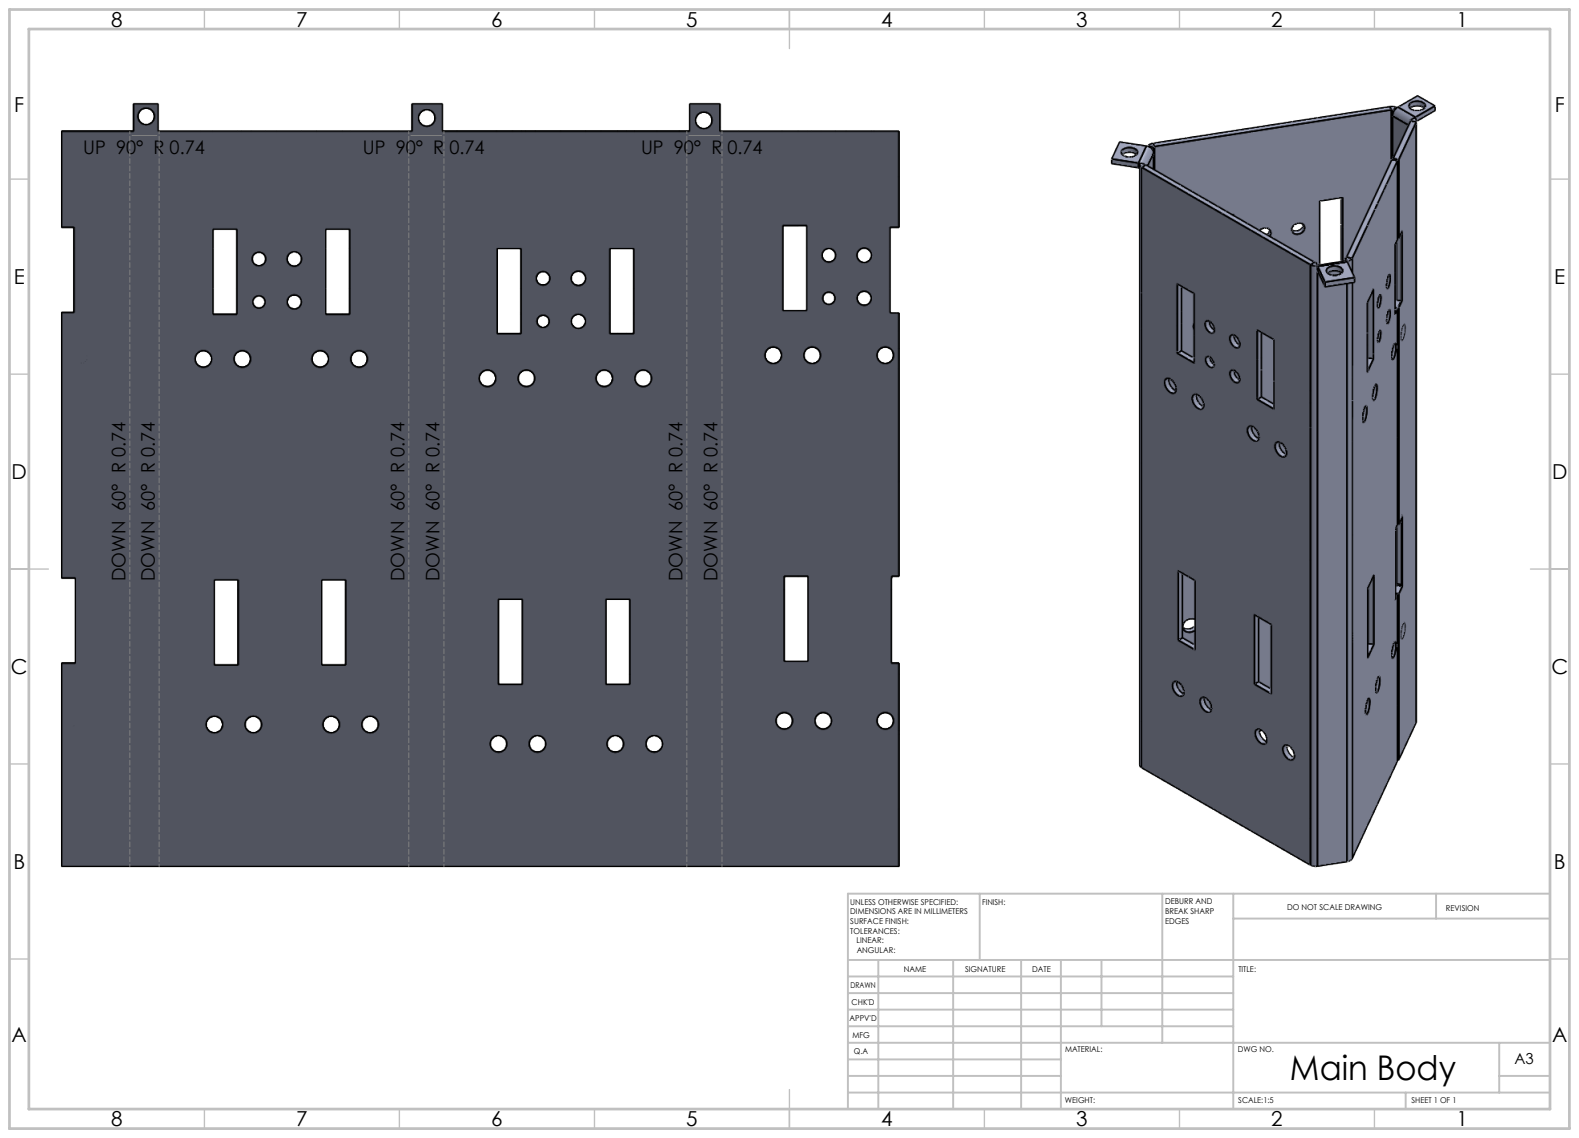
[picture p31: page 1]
DOWN 60° R 0.74; UP 90° R 0.74 DOWN 60° R 0.74; FINISH:; DEBURR AND; BREAK SHARP; DO NOT SCALE DRAWING; REVISION; SCALE:1:5; SHEET 1 OF 1

UNLESS OTHERWISE SPECIFIED:
DIMENSIONS ARE IN MILLIMETERS
SURFACE FINISH:
TOLERANCES:
LINEAR:
ANGULAR:

NAME | SIGNATURE | DATE | | | | TITLE:

DRAWN
CHK'D
APPV'D
MFG
Q.A | | | | MATERIAL: | DWG NO. Main Body | A3

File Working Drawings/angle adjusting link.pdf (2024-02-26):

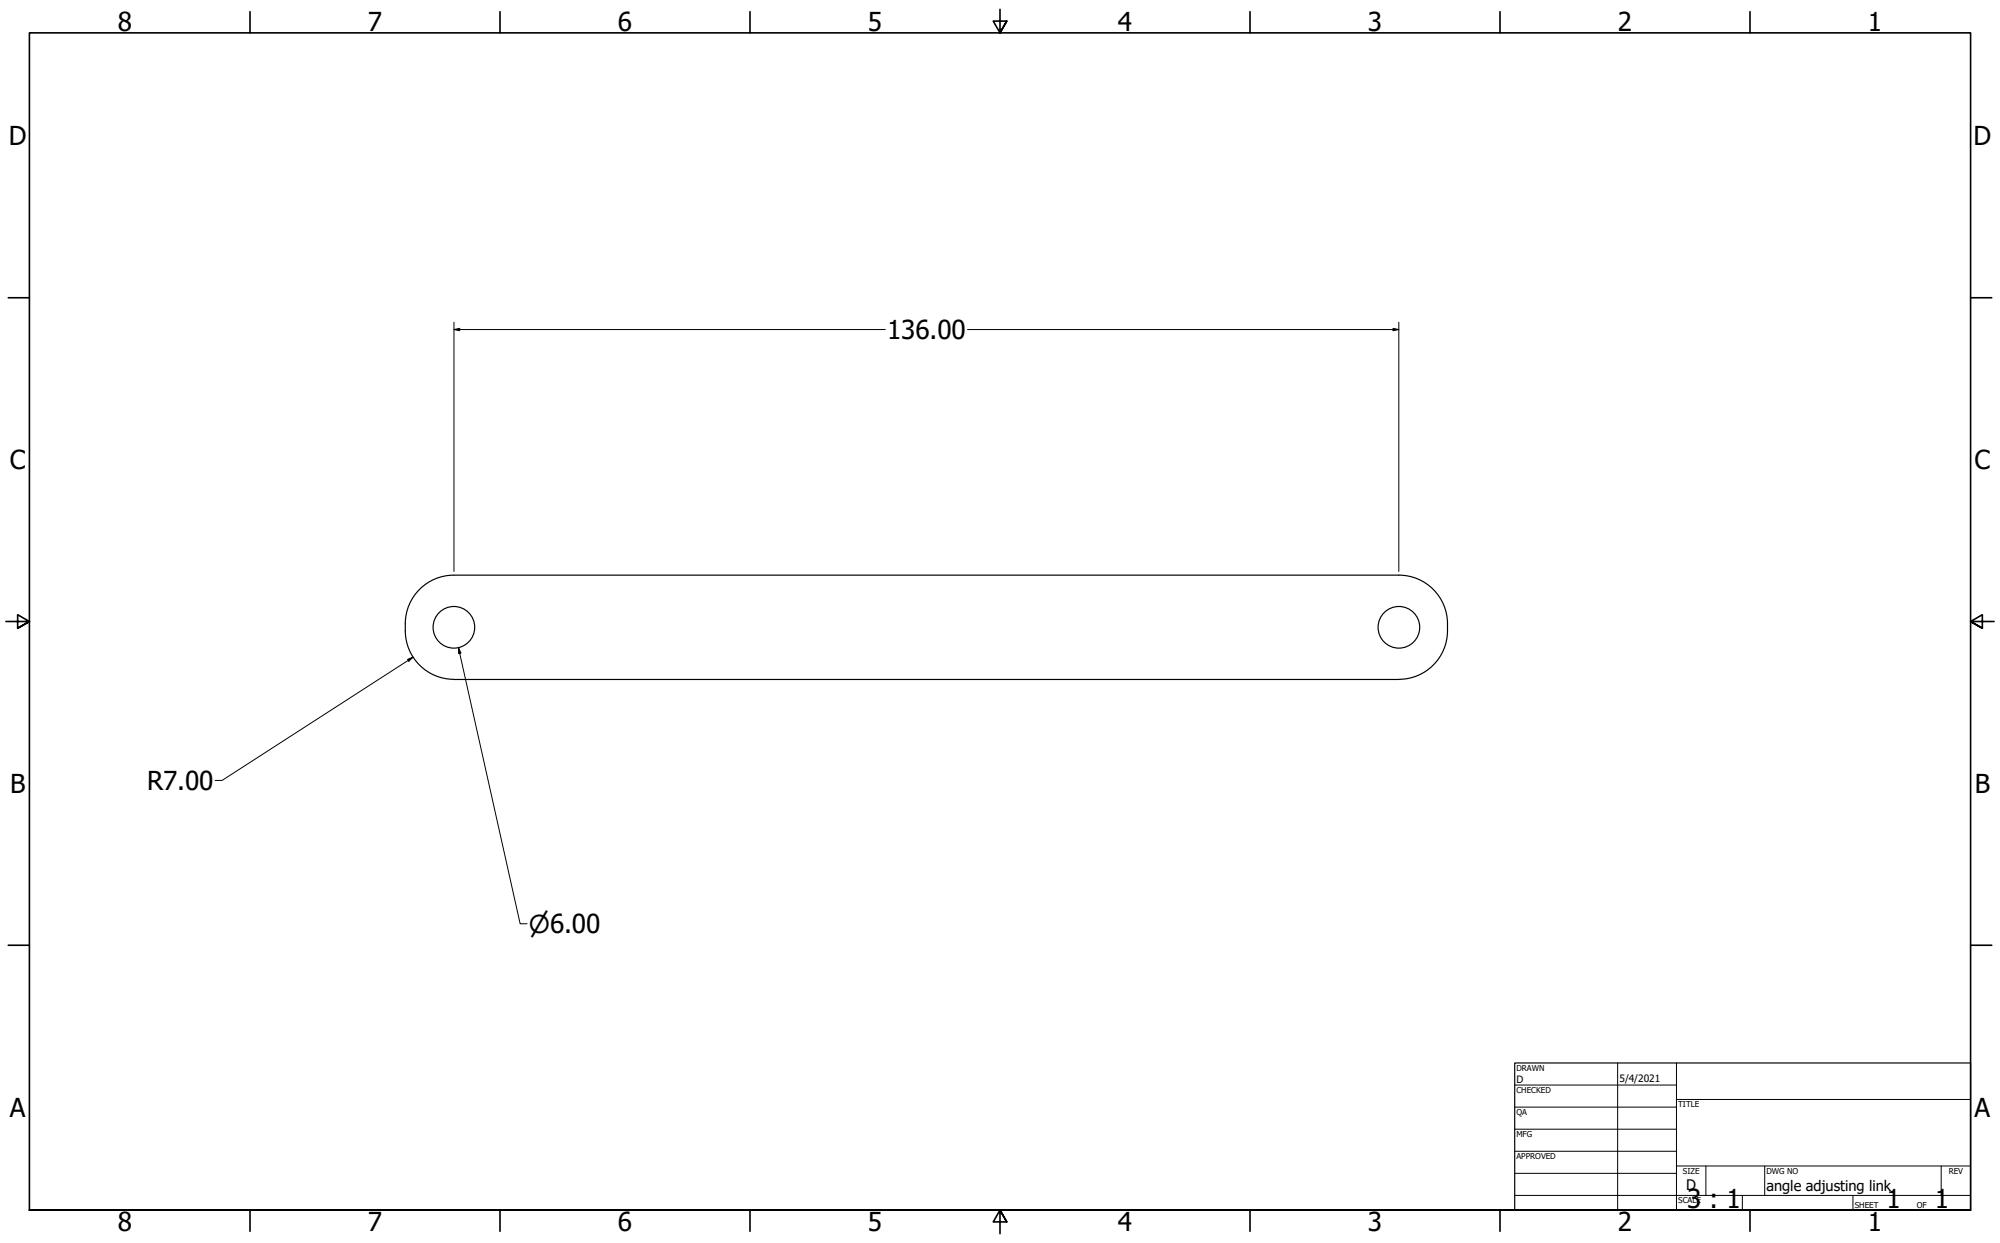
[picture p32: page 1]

DRAWN D | 5/4/2021

CHECKED

MFG

APPROVED

SIZE D | DWG NO angle adjusting link | REV

3 : 1 SCALE | | SHEET 1 OF 1

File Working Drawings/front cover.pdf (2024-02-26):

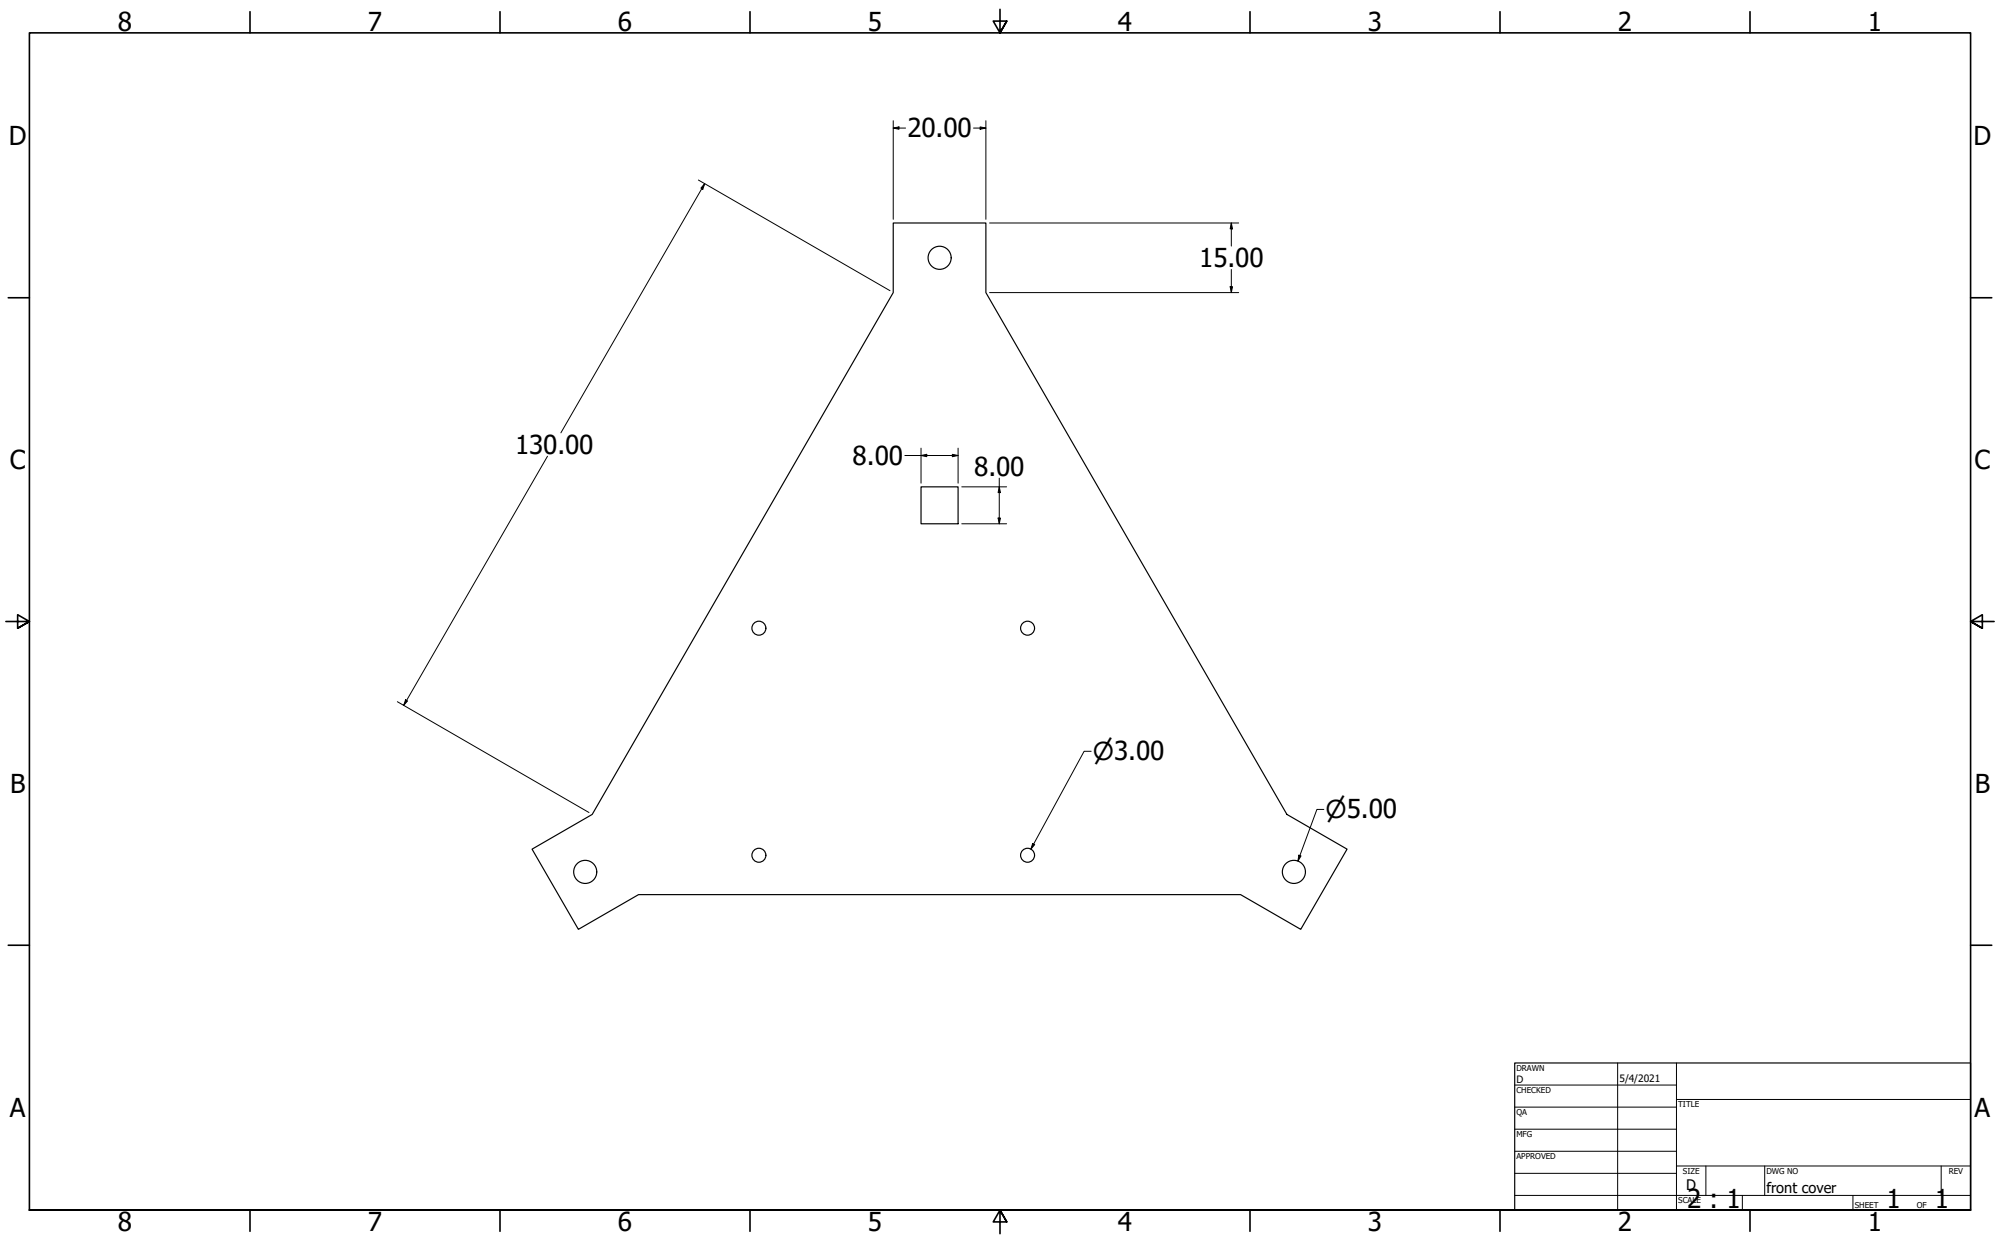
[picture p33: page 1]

DRAWN D | 5/4/2021

CHECKED

MFG

APPROVED

SIZE D | DWG NO front cover | REV

2 : 1 SCALE | | SHEET 1 OF 1

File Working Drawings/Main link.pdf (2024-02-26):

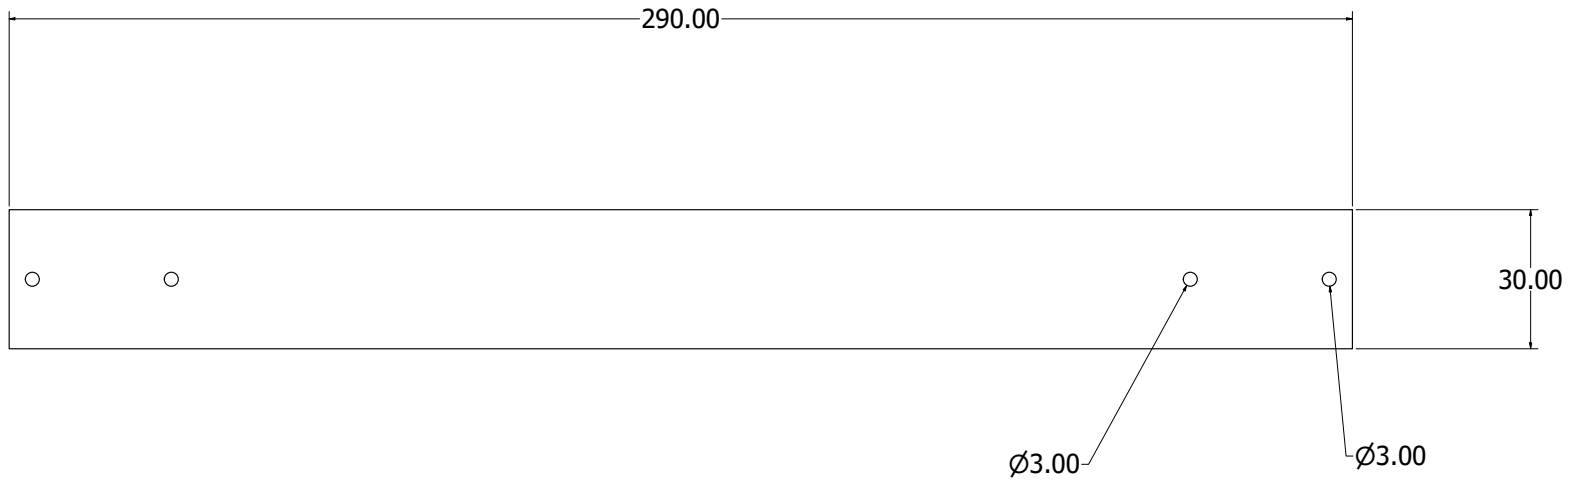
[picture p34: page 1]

DRAWN D | 5/4/2021

CHECKED

MFG

APPROVED

SIZE D | DWG NO Main link | REV

2 : 1 SCALE | | SHEET 1 OF 1

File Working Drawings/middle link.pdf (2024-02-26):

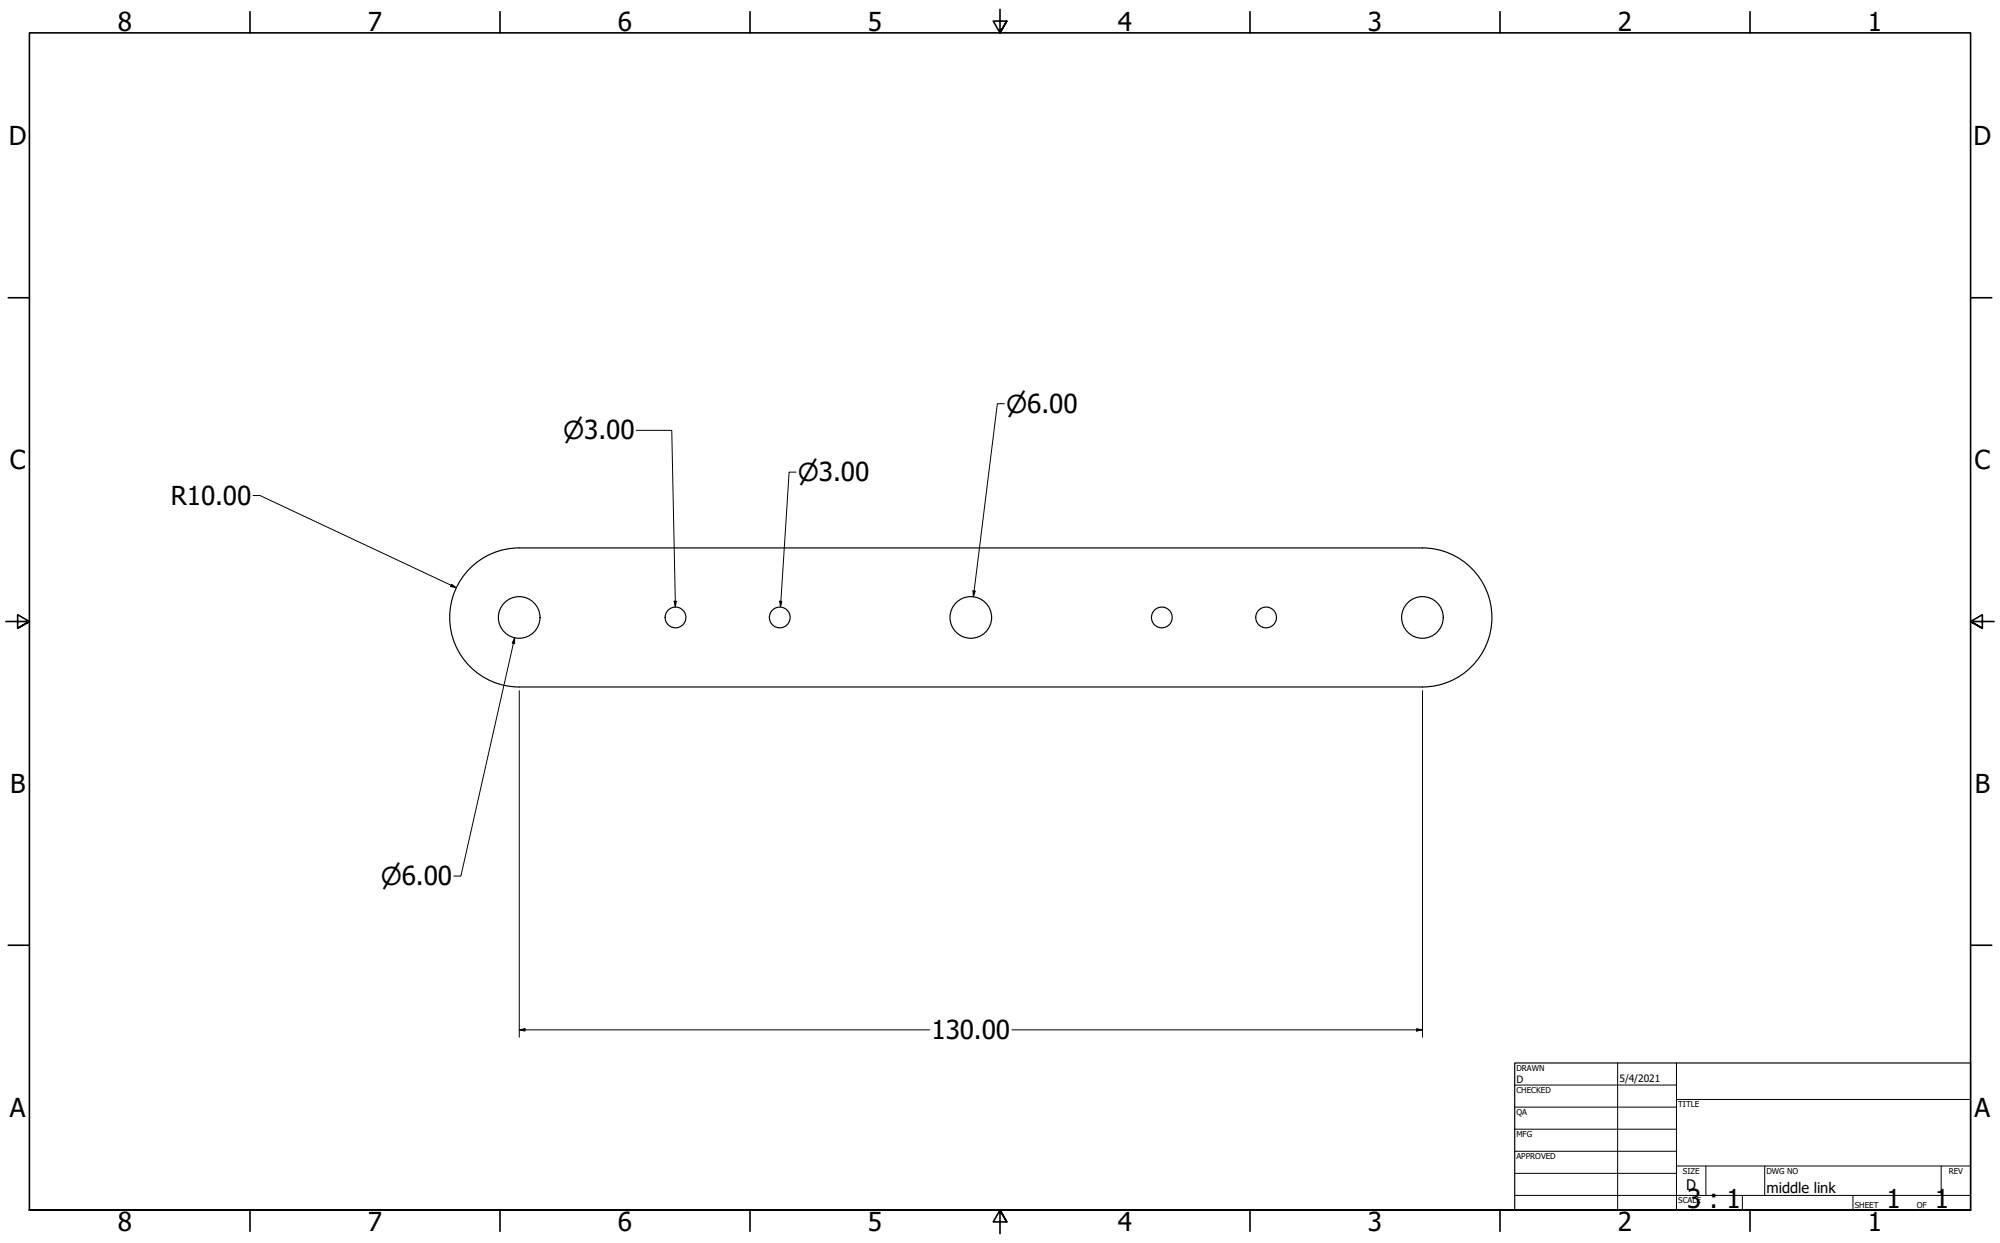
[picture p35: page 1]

DRAWN D | 5/4/2021

CHECKED

MFG

APPROVED

SIZE D | DWG NO middle link | REV

3 : 1 SCALE | | SHEET 1 OF 1

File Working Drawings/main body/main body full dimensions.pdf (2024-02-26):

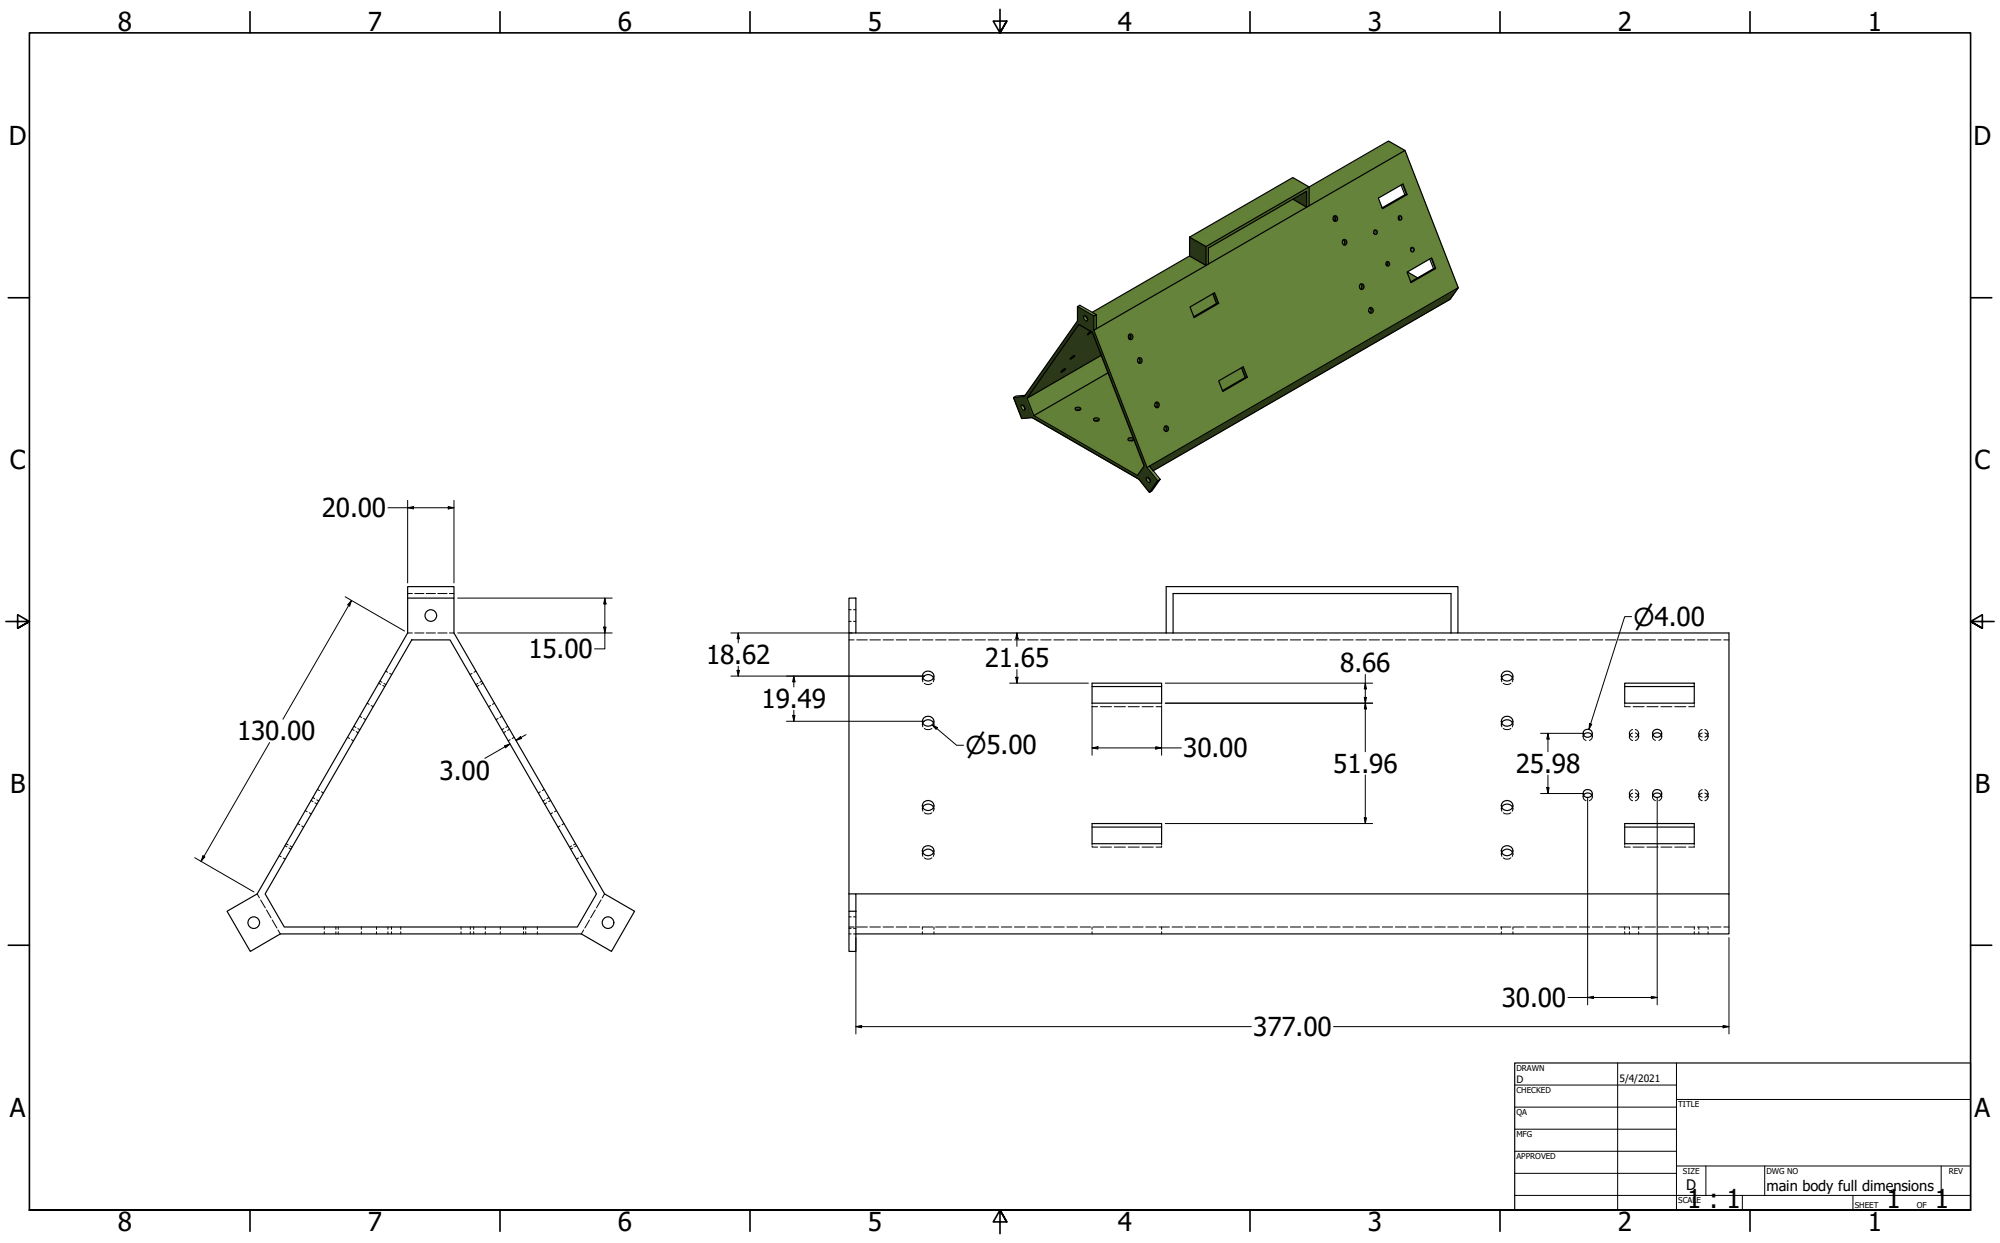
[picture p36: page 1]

DRAWN D | 5/4/2021

CHECKED

MFG

APPROVED

SIZE D | DWG NO main body full dimensions | REV

1 : 1 SCALE | | SHEET 1 OF 1

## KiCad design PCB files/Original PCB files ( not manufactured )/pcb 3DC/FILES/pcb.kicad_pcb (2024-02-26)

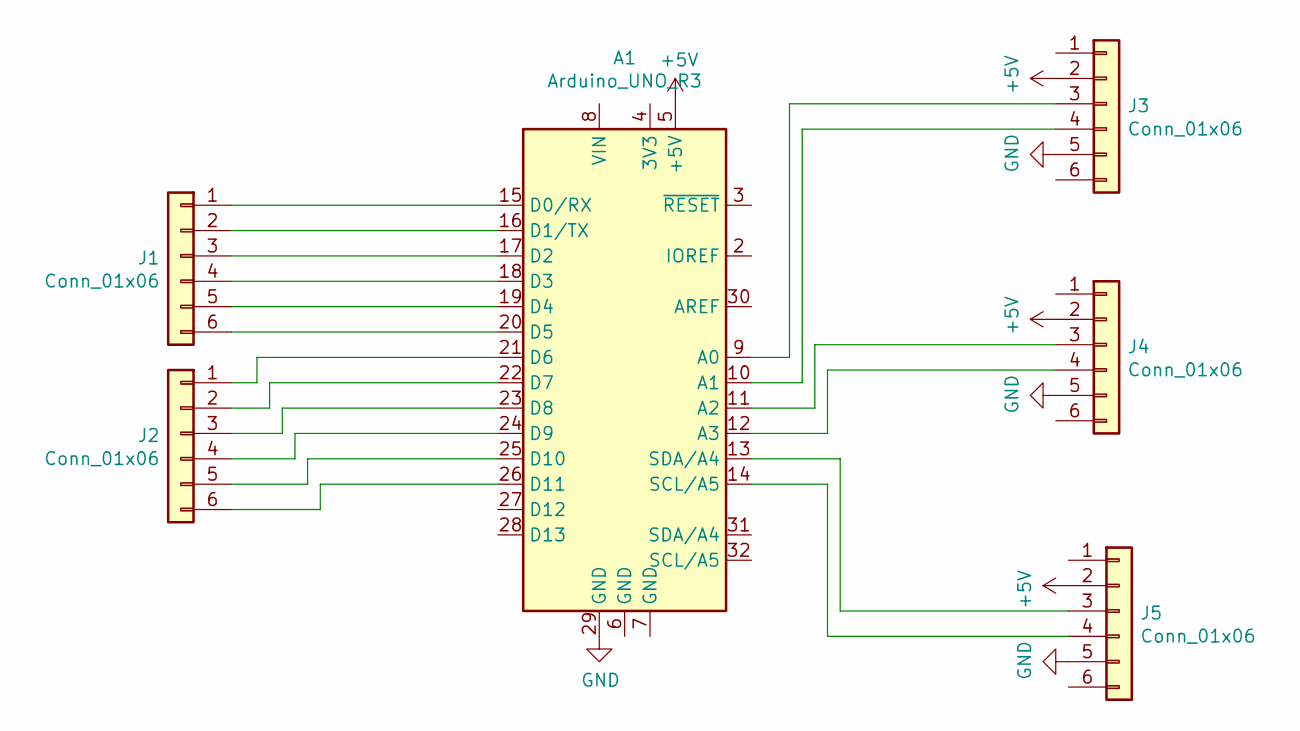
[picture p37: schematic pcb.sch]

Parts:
A1: Arduino_UNO_R3
J1, J2, J3, J4, J5: Conn_01x06; SolderWire-0.1sqmm_1x06_P3.6mm_D0.4mm_OD1mm

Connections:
+5V: A1.5 (+5V), J3.2, J4.2, J5.2
GND: A1.29 (GND), J3.5, J4.5, J5.5
unnamed: A1.9 (A0), J3.3
unnamed: A1.10 (A1), J3.4
unnamed: A1.11 (A2), J4.3
unnamed: A1.12 (A3), J4.4
unnamed: A1.13 (SDA/A4), J5.3
unnamed: A1.14 (SCL/A5), J5.4
unnamed: A1.15 (D0/RX), J1.1
unnamed: A1.16 (D1/TX), J1.2
unnamed: A1.17 (D2), J1.3
unnamed: A1.18 (D3), J1.4
unnamed: A1.19 (D4), J1.5
unnamed: A1.20 (D5), J1.6
unnamed: A1.21 (D6), J2.1
unnamed: A1.22 (D7), J2.2
unnamed: A1.23 (D8), J2.3
unnamed: A1.24 (D9), J2.4
unnamed: A1.25 (D10), J2.5
unnamed: A1.26 (D11), J2.6

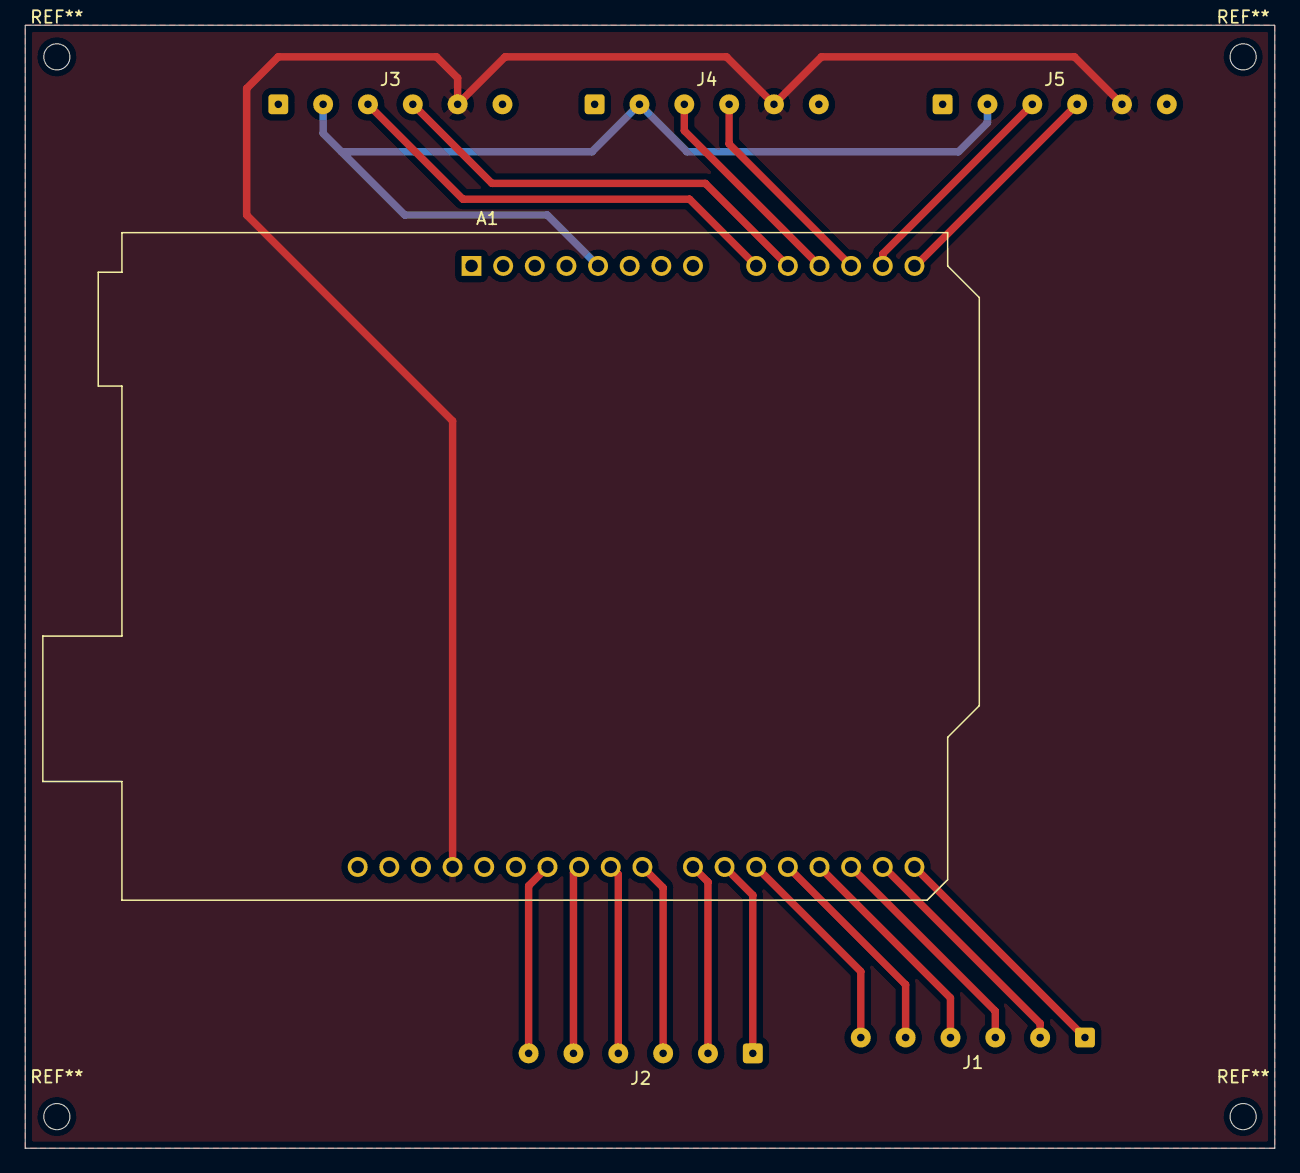
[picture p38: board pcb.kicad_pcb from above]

Board: 2 copper layers, 100.3 x 90.2 mm, 6 parts (0 on the bottom side), 20 nets.

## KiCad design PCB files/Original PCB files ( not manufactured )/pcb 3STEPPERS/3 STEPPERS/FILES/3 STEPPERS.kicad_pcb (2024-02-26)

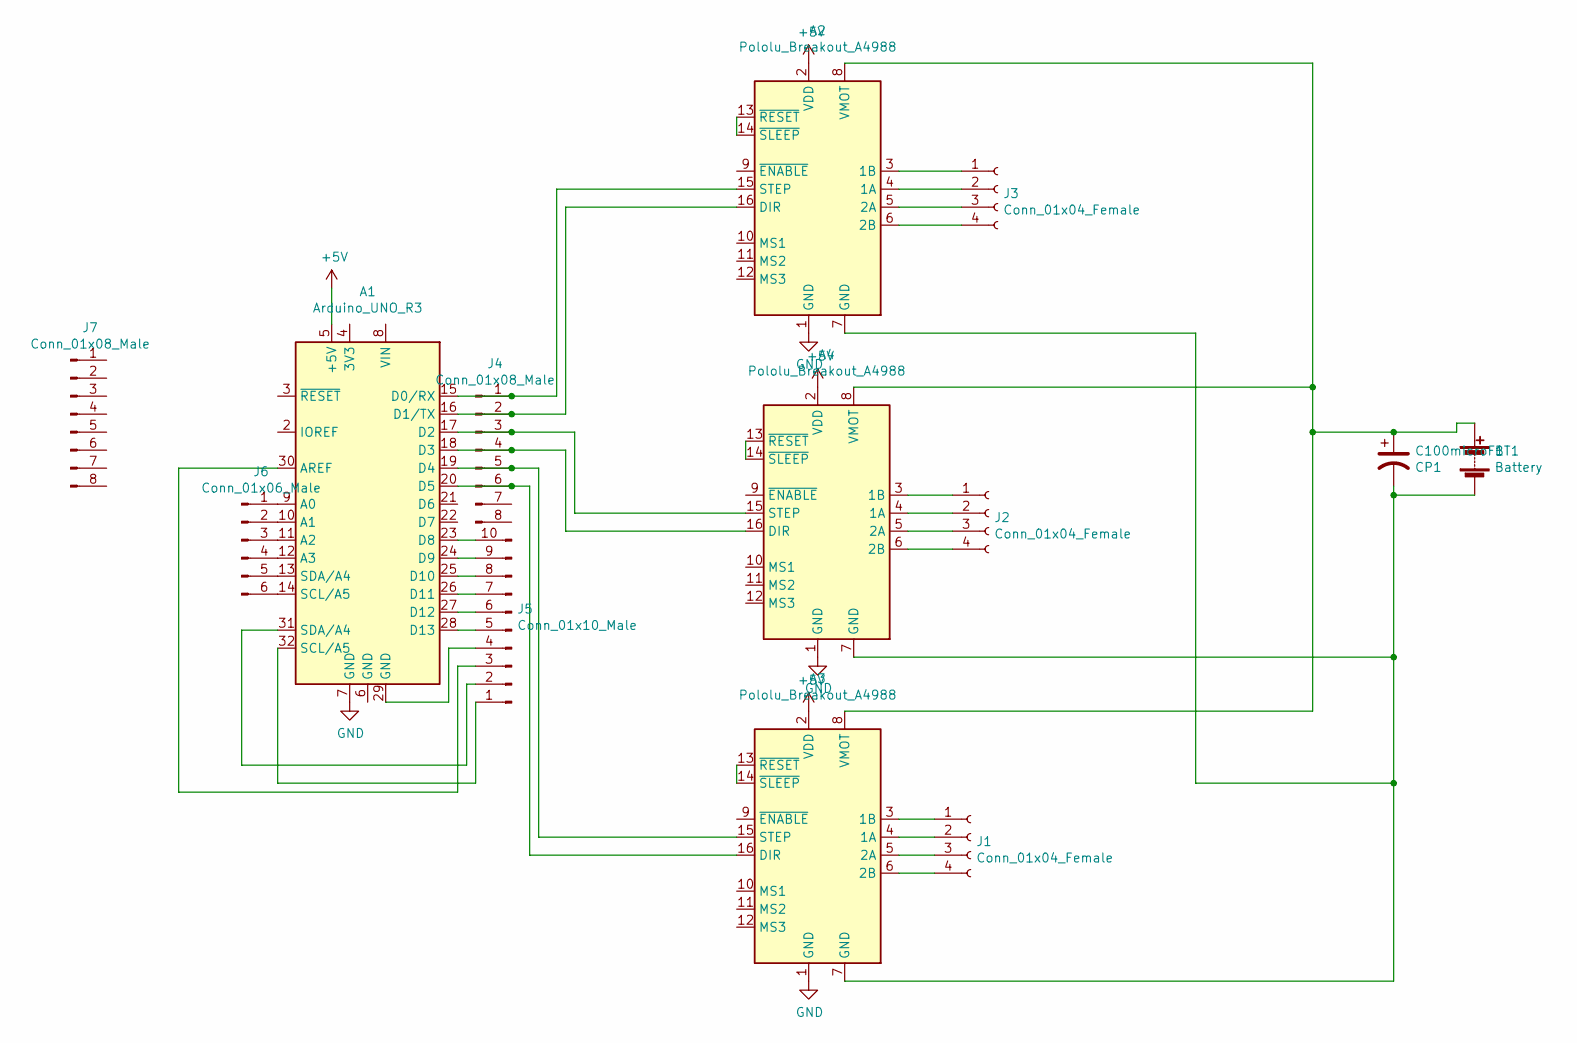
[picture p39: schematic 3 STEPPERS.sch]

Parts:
A1: Arduino_UNO_R3
A2, A3, A4: Pololu_Breakout_A4988; Pololu_Breakout-16_15.2x20.3mm
BT1: Battery; TerminalBlock_Phoenix_MKDS-1,5-2_1x02_P5.00mm_Horizontal
C100microF1: CP1; CP_Radial_D12.5mm_P7.50mm
J1, J2, J3: Conn_01x04_Female; PinSocket_1x04_P1.00mm_Vertical
J4, J7: Conn_01x08_Male; PinHeader_1x08_P2.54mm_Vertical
J5: Conn_01x10_Male; PinHeader_1x10_P2.54mm_Vertical
J6: Conn_01x06_Male; PinHeader_1x06_P2.54mm_Vertical

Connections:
+5V: A1.5 (+5V), A2.2 (VDD), A3.2 (VDD), A4.2 (VDD)
GND: A1.7 (GND), A2.1 (GND), A3.1 (GND), A4.1 (GND)
unnamed: A1.9 (A0), J6.1
unnamed: A1.10 (A1), J6.2
unnamed: A1.11 (A2), J6.3
unnamed: A1.12 (A3), J6.4
unnamed: A1.13 (SDA/A4), J6.5
unnamed: A1.14 (SCL/A5), J6.6
unnamed: A1.15 (D0/RX), A2.15 (STEP), J4.1
unnamed: A1.16 (D1/TX), A2.16 (DIR), J4.2
unnamed: A1.17 (D2), A4.15 (STEP), J4.3
unnamed: A1.18 (D3), A4.16 (DIR), J4.4
unnamed: A1.19 (D4), A3.15 (STEP), J4.5
unnamed: A1.20 (D5), A3.16 (DIR), J4.6
unnamed: A1.23 (D8), J5.10
unnamed: A1.24 (D9), J5.9
unnamed: A1.25 (D10), J5.8
unnamed: A1.26 (D11), J5.7
unnamed: A1.27 (D12), J5.6
unnamed: A1.28 (D13), J5.5
unnamed: A1.29 (GND), J5.4
unnamed: A1.30 (AREF), J5.3
unnamed: A1.31 (SDA/A4), J5.2
unnamed: A1.32 (SCL/A5), J5.1
unnamed: A2.3 (1B), J3.1
unnamed: A2.4 (1A), J3.2
unnamed: A2.5 (2A), J3.3
unnamed: A2.6 (2B), J3.4
unnamed: A2.7 (GND), A3.7 (GND), A4.7 (GND), BT1.2 (-), C100microF1.2
unnamed: A2.8 (VMOT), A3.8 (VMOT), A4.8 (VMOT), BT1.1 (+), C100microF1.1
unnamed: A2.13 (~RESET), A2.14 (~SLEEP)
unnamed: A3.3 (1B), J1.1
unnamed: A3.4 (1A), J1.2
unnamed: A3.5 (2A), J1.3
unnamed: A3.6 (2B), J1.4
unnamed: A3.13 (~RESET), A3.14 (~SLEEP)
unnamed: A4.3 (1B), J2.1
unnamed: A4.4 (1A), J2.2
unnamed: A4.5 (2A), J2.3
unnamed: A4.6 (2B), J2.4
unnamed: A4.13 (~RESET), A4.14 (~SLEEP)

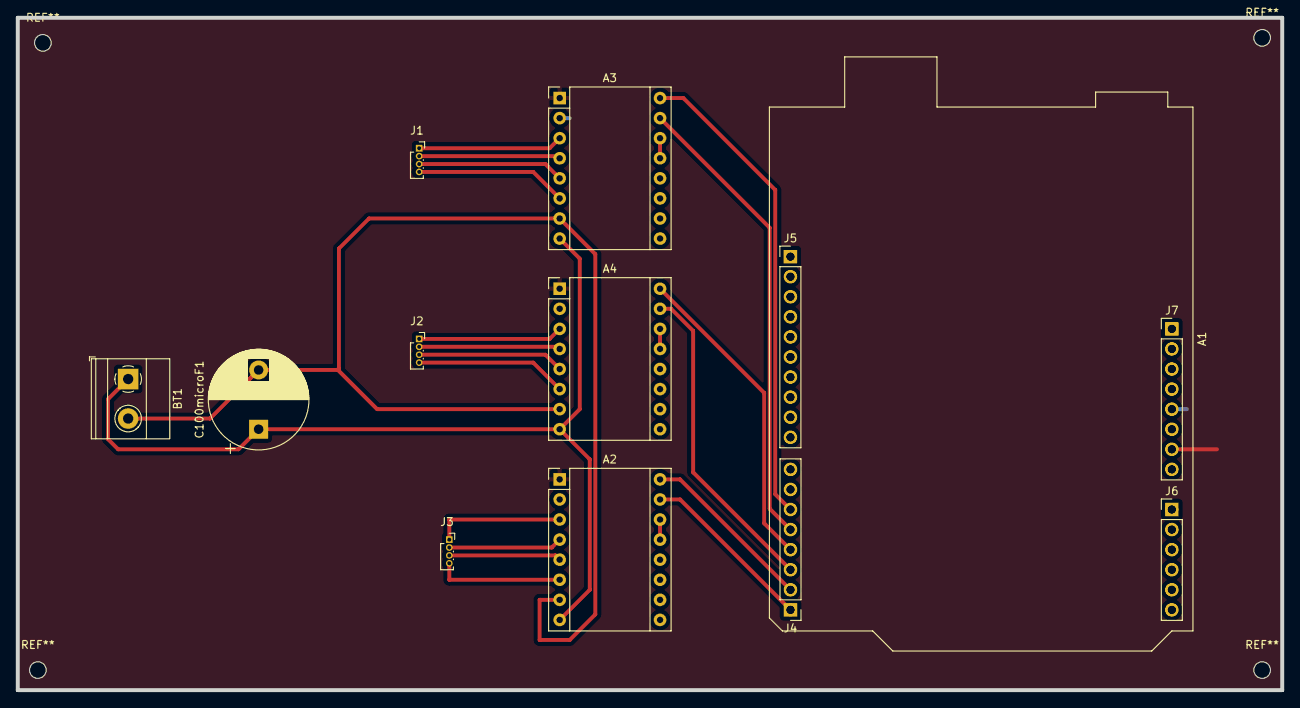
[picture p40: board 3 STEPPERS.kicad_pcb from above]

Board: 2 copper layers, 160.0 x 85.1 mm, 13 parts (0 on the bottom side), 41 nets.

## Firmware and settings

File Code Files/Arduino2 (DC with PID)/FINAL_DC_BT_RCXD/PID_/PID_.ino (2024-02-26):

#include <PID_v1.h>
#include <TimerOne.h>
#include <Wire.h>
 


//VARIABLES

int speed_R = 255;
int distance_F=0;
int distance_B=0;

int dis = 0;
char com;
int n =1;
int ON_F = 0;
int ON_B = 0;

char pi_state='a';

int enc1 = 2;
int enc2 = 3;

double R_pwmOutput = 0 ;
double R_SpeedRPM = 0.0;

double Setpoint = 140;

float R_Kp = 1.1, R_Ki = 4.8, R_Kd = 0.05;
//float R_Kp = 5, R_Ki = 30, R_Kd = 0.05;

volatile unsigned long counter1 = 0;

const float ppr = 400.0/10;



//HANDLES....................................................

PID R_rpm(&R_SpeedRPM, &R_pwmOutput, &Setpoint, R_Kp, R_Ki , R_Kd, DIRECT ) ;




//MACROS.....................................................

// Define Slave I2C Address
  #define SLAVE_ADDR 9
 
// Define Slave answer size
  #define ANSWERSIZE 5

#define DC_1_F 13 //forward=1
#define DC_1_B 12 //backward=1
#define DC_1_EN 11 



//FUNCTION PROTOTYPES........................................

void RC_F();
void RC_B();
void RC_STOP();
void int_timer();
void int_count1();
void receiveEvent();

void setup() {
  // put your setup code here, to run once:
  pinMode(DC_1_EN, OUTPUT);
  pinMode(DC_1_F, OUTPUT);
  pinMode(DC_1_B, OUTPUT);

  // Initialize I2C communications as Slave
  Wire.begin(SLAVE_ADDR);
   
  // Function to run when data received from master
  Wire.onReceive(receiveEvent);
  
  Serial.begin(9600);
  
 
  Timer1.initialize(100000);
      attachInterrupt(digitalPinToInterrupt(enc1),int_count1, RISING);
 
      R_rpm.SetMode(AUTOMATIC);
 
    
}


void loop() {
  // put your main code here, to run repeatedly:

  while(1)
  {
    Serial.print(" in loop \n");
    delay(2000);
    if (dis!=0)
    {
        Timer1.attachInterrupt(int_timer);
    break;
    }
  }
  
  delay(500);
 Serial.print("distance = ");
 Serial.println(dis);
 
if(com=='e' )
{
  
while(dis!=0)
{
  
 RC_B();
      distance_B--;
      delay(1000);
      if (distance_B ==0)
      {
        ON_B=0;
        RC_STOP();
        delay(5000);
       break;
    
      } 
}
}

 delay(2000);
 
  
if(dis != 0)
{
  ON_F=1;
  
  distance_F = dis;
  
  distance_B = distance_F;

  while ( ON_F == 1)
   {
    if(Serial.available() > 0)
  { 
      pi_state = Serial.read();
  }
   
      RC_F();
      distance_F--;
      
      Serial.print(" Forward\n");
      Serial.print(distance_F);
      
      delay(1000);
           
     if(pi_state=='q')
      {
        RC_F_SLOW();
        
        pi_state='a';
        
      }
        if (distance_F ==0)
        {
          // Timer1.detachInterrupt();
            RC_STOP();
          ON_F=0;
          ON_B=1;
        
           Serial.print(" REACHED DISTNATION \n");
          delay(5000);
          break;
      
        }

   }

    while ( ON_B == 1)
   {
   
      RC_B();
      distance_B--;

       Serial.print(" Backward\n");
      Serial.print(distance_B);
      
      delay(1000);
      if (distance_B ==0)
      {
        ON_B=0;
        // Timer1.detachInterrupt();
        RC_STOP();
        dis=0;
         Serial.print(" REACHED DISTNATION \n");
         dis=0;
        delay(5000);
        break;
    
      } 
}
}

}

//FUNCTIONS DEFINITION
//////////////////////////////////////////////////////

void RC_F()
{
  //analogWrite(DC_1_EN,speed_R);

   digitalWrite(DC_1_F,HIGH);
    digitalWrite(DC_1_B,LOW);
  
}

//////////////////////////////////////////////////////

void RC_F_SLOW()
{
   Setpoint = 50;
   delay(5000);
    Setpoint = 140;
  
}

//////////////////////////////////////////////////////

void RC_B()
{
  analogWrite(DC_1_EN,speed_R);

   digitalWrite(DC_1_B,HIGH);
   digitalWrite(DC_1_F,LOW);
  
}

//////////////////////////////////////////////////////

void RC_STOP()
{
   Timer1.detachInterrupt();
   digitalWrite(DC_1_B,LOW);
   digitalWrite(DC_1_F,LOW);
}

//////////////////////////////////////////////////////

void int_timer(){
  Timer1.detachInterrupt();
  R_SpeedRPM = (counter1/ppr)*60.0;
  R_rpm.Compute();
  analogWrite (DC_1_EN , R_pwmOutput );
  Serial.print("motor 1 speed : ");
  Serial.println(R_SpeedRPM);
  Serial.println(Setpoint);
  counter1 = 0;
 
  Timer1.attachInterrupt(int_timer);
}

//////////////////////////////////////////////////////

void int_count1(){
  counter1++;
}

//////////////////////////////////////////////////////


void receiveEvent() {
 
  // Read while data received
  while (0 < Wire.available()) {
    dis = Wire.read();
  }
  Serial.println("Receive event");
}
